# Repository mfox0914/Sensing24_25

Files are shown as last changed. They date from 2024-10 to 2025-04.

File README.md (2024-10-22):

# Olin Baja - 2022-2023 Electrical Projects

A variety of KiCAD schematics, PCBs, and other fun stuff from your favorite offroad vehicle team at Olin Collge of Engineering

## Current Projects
* SPI to CAN Board
	* Adapter board to convert from SPI sensor signals to CAN signals using a Raspberry Pi Pico
* Tachometer Board
	* Attempting to ressurect a techometer circut from a Baja project long ago.

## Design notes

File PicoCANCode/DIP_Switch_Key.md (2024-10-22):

## 2022 Olin Baja - DIP Switch Guide
DIP switches are assumed to be pulled LOW when active.

.

### **Ride Height - Front Driver Side**
DIP0        DIP1     DIP2        DIP3

0           0        0           0

CAN Address: 0x1111FFAA

### **Ride Height - Front Passenger Side**
DIP0        DIP1     DIP2        DIP3

1           0        0           0

CAN Address: 0x1111FFBB

### **Ride Height - Rear Driver Side**
DIP0        DIP1     DIP2        DIP3

0           1        0           0

CAN Address: 0x1111EEAA

### **Ride Height - Rear Passenger Side**
DIP0        DIP1     DIP2        DIP3

0           0        1           0

CAN Address: 0x1111EEBB

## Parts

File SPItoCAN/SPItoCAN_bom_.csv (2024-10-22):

Component | Description | Part | References | Value | Footprint | Quantity Per PCB | Datasheet | MFN | MPN | PurchasingLink | Digikey PN | Purchase Link
1 | Capacitor, 0.1uF, 50V, 5%, 0805 | C_0.1uF | C4 C5 | C_0.1uF | C_0805_OEM | 2 | http://datasheets.avx.com/X7RDielectric.pdf | DK | 478-3352-1-ND | https://www.digikey.com/products/en?keywords=478-3352-1-ND
2 | Capacitor, 10uF, 16V, 10%, 0805 | C_10uF_16V | C3 | C_10uF_16V | C_0805_OEM | 1 | http://www.samsungsem.com/kr/support/product-search/mlcc/__icsFiles/afieldfile/2016/01/15/Data%20sheet_CL21A106KOCLRNC.pdf | DK | 1276-2399-1-ND | https://www.digikey.com/product-detail/en/samsung-electro-mechanics/CL21A106KOCLRNC/1276-2399-1-ND/3890485
3 | Capacitor, 18pF, 10V, 1%, 0603 | C_18pF | C1 C2 | C_22pF | C_0603_1608Metric | 2 | https://www.vishay.com/docs/28548/vjw1bcbascomseries.pdf | DK | 720-1660-1-ND | https://www.digikey.com/product-detail/en/vishay-vitramon/VJ0603A180FXQCW1BC/720-1660-1-ND/8324080
4 | LED_0805_Red | LED_0805_Red | D1 | LED_0805_Red | LED_0805_Red | 1 | https://docs.broadcom.com/docs/AV02-0112EN | Avago | HSMC-C170 | https://www.digikey.com/product-detail/en/osram-opto-semiconductors-inc/LH-R974-LP-1/475-1415-1-ND/1802604 | 516-1428-1-ND
5 | CONN HEADER 2 POS 2.54mm | CONN_01x02 | J1 J2 J3 | CONN_01x02 | PinHeader_1x02_P2.54mm_Vertical | 3 | https://katalog.we-online.de/em/datasheet/6130xx11121.pdf | DK | 732-5315-ND
6 |  | Conn_01x07 | J4 | Conn_01x07 | PinHeader_1x07_P2.54mm_Vertical | 1 | https://www.we-online.com/katalog/datasheet/6130xx11121.pdf | Würth Elektronik | 61300711121 | https://www.digikey.com/en/products/detail/61300711121/732-5320-ND/4846837?curr=usd
7 |  | R_10K | R1 | R_10K | R_0805_OEM | 1 | http://www.bourns.com/data/global/pdfs/CRS.pdf | DK | CRS0805-FX-1002ELFCT-ND | https://www.digikey.com/products/en?keywords=CRS0805-FX-1002ELFCT-ND
8 |  | R_120 | R2 | R_120 | R_0805_OEM | 1 | https://www.mouser.com/datasheet/2/315/AOA0000C304-1149620.pdf | DK | 667-ERJ-6ENF1200V | https://www.mouser.com/ProductDetail/Panasonic-Industrial-Devices/ERJ-6ENF1200V
9 |  | R_1K | R3 | R_1K | R_0805_OEM | 1 | https://www.seielect.com/Catalog/SEI-rncp.pdf | DK | RNCP0805FTD1K00CT-ND | https://www.digikey.com/products/en?keywords=RNCP0805FTD1K00CT-ND
10 | Stand-Alone CAN Controller with SPI Interface, SOIC-18 | MCP2515-xSO | U2 | MCP2515-xSO | SOIC-18W_7.5x11.6mm_P1.27mm | 1 | https://ww1.microchip.com/downloads/en/DeviceDoc/MCP2515-Stand-Alone-CAN-Controller-with-SPI-20001801J.pdf |  | MCP2515T-I/SO | https://www.digikey.com/en/products/detail/microchip-technology/MCP2515T-I-SO/593681 | MCP2515T-I/SODKR-ND
11 |  | TJA1050T | U1 | TJA1051T-E | SOIC127P600X175-8N | 1 | https://www.mouser.com/datasheet/2/302/TJA1050-1127967.pdf |  | TJA1050T/CM,118 | https://www.mouser.com/ProductDetail/NXP-Semiconductors/TJA1050T-CM118?qs=5XOdhvmYM0NFFspw0VP5sA%3D%3D
12 | CRYSTAL 8.0000MHZ 18PF SMD | Crystal_8MHz | Y1 | Crystal_8MHz | ABM3-8_5.0x3.2mm_P3.7mm | 1 | https://abracon.com/Resonators/abm3.pdf | DK | 535-10630-1-ND | https://www.digikey.com/product-detail/en/abracon-llc/ABM3-8.000MHZ-D2Y-T/535-10630-1-ND/2344632
Component Groups: | 12
Component Count: | 16
Fitted Components: | 16
Number of PCBs: | 1
Total components: | 16
Schematic Version:
Schematic Date:
PCB Variant: | default
BoM Date: | 1/25/2023 20:43
Schematic Source: | SPItoCAN.kicad_sch
KiCad Version: | Eeschema (6.0.7)

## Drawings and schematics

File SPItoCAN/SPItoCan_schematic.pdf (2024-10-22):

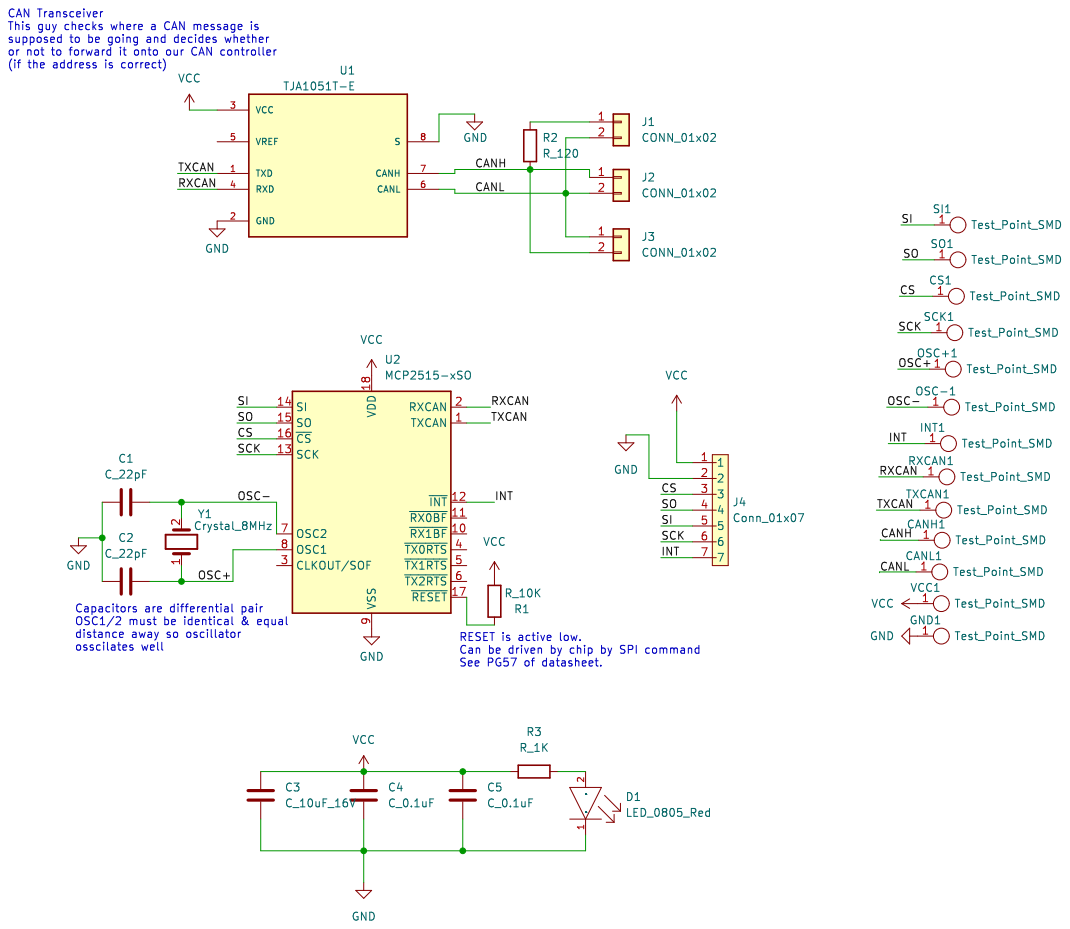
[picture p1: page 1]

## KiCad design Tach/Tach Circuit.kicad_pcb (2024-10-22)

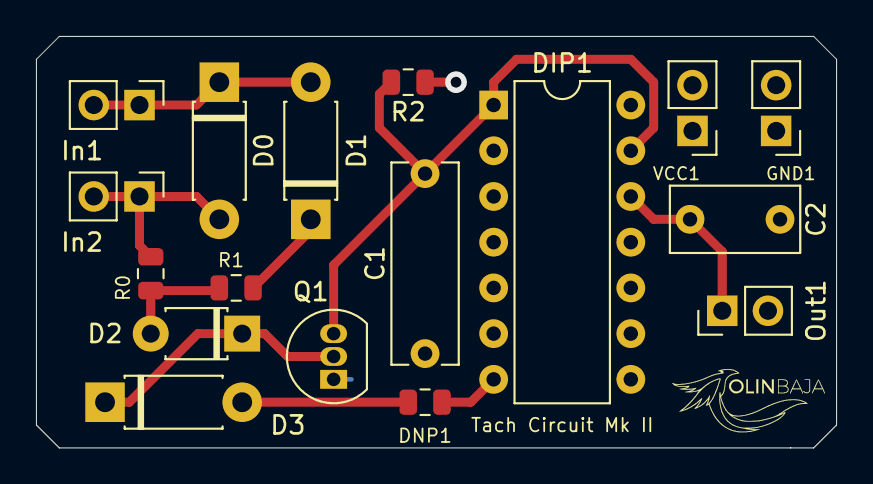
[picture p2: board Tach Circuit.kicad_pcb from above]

Board: 2 copper layers, 44.4 x 22.9 mm, 17 parts (0 on the bottom side), 10 nets.

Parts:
C1: 2200pF; C_Rect_L11.0mm_W3.5mm_P10.00mm_MKT
C2: 39nF; C_Rect_L7.0mm_W3.5mm_P5.00mm
D0, D1: 1N4007; D_DO-41_SOD81_P7.62mm_Horizontal
D2: 1N4148; D_T-1_P5.08mm_Horizontal
D3: 1N4738; D_DO-41_SOD81_P7.62mm_Horizontal
DIP1: SN74HC14N; DIP-14_W7.62mm
DNP1: DNP; R_0805_2012Metric
GND1: GND; PinHeader_1x02_P2.54mm_Vertical
In1: Vin +; PinHeader_1x02_P2.54mm_Vertical
In2: Vin-; PinHeader_1x02_P2.54mm_Vertical
Out1: Vout; PinHeader_1x02_P2.54mm_Vertical
Q1: 2N3904; TO-92_Inline
R0, R1: 10k; R_0805_2012Metric
R2: 4.7k; R_0805_2012Metric
VCC1: 5V; PinHeader_1x02_P2.54mm_Vertical

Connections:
+5V: DIP1.14, R2.1, VCC1.1
GND: C1.2, C2.2, DIP1.7, DNP1.2, GND1.1, Q1.1
unnamed: C1.1, DIP1.1, DIP1.13, Q1.3, R2.2
unnamed: C2.1, DIP1.12, Out1.1
unnamed: D0.1, D1.2, In1.1
unnamed: D0.2, In2.1, R0.1
unnamed: D1.1, R1.2
unnamed: D2.1, D3.1, Q1.2
unnamed: D2.2, R0.2, R1.1
unnamed: D3.2, DNP1.1

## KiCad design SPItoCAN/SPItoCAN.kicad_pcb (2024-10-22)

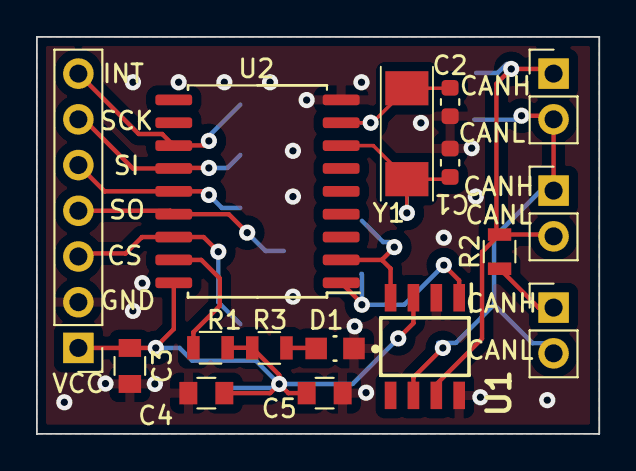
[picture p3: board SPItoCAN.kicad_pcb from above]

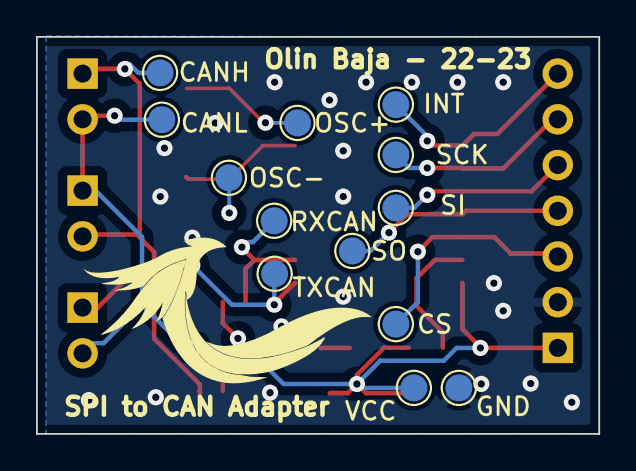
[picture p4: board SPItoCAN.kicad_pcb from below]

Board: 2 copper layers, 31.2 x 22.1 mm, 29 parts (13 on the bottom side), 16 nets.

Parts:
C1, C2: C_22pF; C_0603_1608Metric
C3: C_10uF_16V; C_0805_OEM
C4, C5: C_0.1uF; C_0805_OEM
CANH: Test_Point_SMD; TestPoint_Pad_D1.5mm
CANL: Test_Point_SMD; TestPoint_Pad_D1.5mm
CS: Test_Point_SMD; TestPoint_Pad_D1.5mm
D1: LED_0805_Red
GND: Test_Point_SMD; TestPoint_Pad_D1.5mm
INT: Test_Point_SMD; TestPoint_Pad_D1.5mm
J1, J2, J3: CONN_01x02; PinHeader_1x02_P2.54mm_Vertical
J4: Conn_01x07; PinHeader_1x07_P2.54mm_Vertical
OSC+: Test_Point_SMD; TestPoint_Pad_D1.5mm
OSC-: Test_Point_SMD; TestPoint_Pad_D1.5mm
R1: R_10K; R_0805_OEM
R2: R_120; R_0805_OEM
R3: R_1K; R_0805_OEM
RXCAN: Test_Point_SMD; TestPoint_Pad_D1.5mm
SCK: Test_Point_SMD; TestPoint_Pad_D1.5mm
SI: Test_Point_SMD; TestPoint_Pad_D1.5mm
SO: Test_Point_SMD; TestPoint_Pad_D1.5mm
TXCAN: Test_Point_SMD; TestPoint_Pad_D1.5mm
U1: TJA1051T-E; SOIC127P600X175-8N
U2: MCP2515-xSO; SOIC-18W_7.5x11.6mm_P1.27mm
VCC: Test_Point_SMD; TestPoint_Pad_D1.5mm
Y1: Crystal_8MHz; ABM3-8_5.0x3.2mm_P3.7mm

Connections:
/CANH: CANH.1, J2.1, J3.2, R2.2, U1.7 (CANH)
/CANL: CANL.1, J1.2, J2.2, J3.1, U1.6 (CANL)
/CS: CS.1, J4.3, U2.16 (~CS)
/INT: INT.1, J4.7, U2.12 (~INT)
/OSC+: C2.2, OSC+.1, U2.8 (OSC1), Y1.1
/OSC-: C1.2, OSC-.1, U2.7 (OSC2), Y1.2
/RXCAN: RXCAN.1, U1.4 (RXD), U2.2 (RXCAN)
/SCK: J4.6, SCK.1, U2.13 (SCK)
/SI: J4.5, SI.1, U2.14 (SI)
/SO: J4.4, SO.1, U2.15 (SO)
/TXCAN: TXCAN.1, U1.1 (TXD), U2.1 (TXCAN)
GND: C1.1, C2.1, C3.2, C4.2, C5.2, D1.1 (CATHODE), GND.1, J4.2, U1.2 (GND), U1.8 (S), U2.9 (VSS)
unnamed: D1.2 (ANODE), R3.2
unnamed: J1.1, R2.1
unnamed: R1.1, U2.17 (~RESET)
VCC: C3.1, C4.1, C5.1, J4.1, R1.2, R3.1, U1.3 (VCC), U2.18 (VDD), VCC.1

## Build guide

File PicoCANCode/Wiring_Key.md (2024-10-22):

# Olin Baja 2022 - Pico Wiring Key

## **DIP Switches**

GP11 - DIP0

GP10 - DIP1

GP9 - DIP2

GP8 - DIP3

(with all other sides of the DIP switch being connected to GND)

## **SPI to CAN Module**

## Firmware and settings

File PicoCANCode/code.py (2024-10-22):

from time import sleep
import board
import busio
from digitalio import DigitalInOut, Direction, Pull
from adafruit_mcp2515.canio import Message, RemoteTransmissionRequest
from adafruit_mcp2515 import MCP2515 as CAN
from analogio import AnalogIn

# Dictionary to convert between DIP switch positions and CAN IDs. Keys are
# tuples representing the values of 4 DIP switches.
#
# Pins default being pulled high, so a pin is pulled to GND and represented by
# "false" when the DIP switch is toggled on
DIP_TO_CAN_ID = {
    (True, True, True, True)  : 0x1111FFAA,
    (False, True, True, True) : 0x1111FFBB,
    (True, False, True, True) : 0x1111EEAA,
    (True, True, False, True) : 0x1111EEBB
}

# Configure DIP Switch inputs
dip0 = DigitalInOut(board.GP11)
dip1 = DigitalInOut(board.GP10)
dip2 = DigitalInOut(board.GP9)
dip3 = DigitalInOut(board.GP8)

# Add all DIP switches to a list to make it easier to assign properties to each
dip_switches = [dip0, dip1, dip2, dip3]

# Define ride height sensor analog input pin
sensor_in = AnalogIn(board.A0)

for switch in dip_switches:
    # Set each DIP switch as an input
    switch.direction = Direction.INPUT
    # Use an integrated pull-up resistor to prevent pins from floating; requires
    # pins to be pulled to GND in order to be active
    switch.pull = Pull.UP

# Determine CAN address (board identity) based on DIP switch position
dip_positions = (dip0.value, dip1.value, dip2.value, dip3.value)
try:
    can_id = DIP_TO_CAN_ID[dip_positions]
    print(f"Successfully set CAN ID. Current ID is: f{can_id}")
except KeyError:
    print("Invalid DIP position. Defaulting to CAD address of 0x00000000")
    can_id = "0x00000000"



cs = DigitalInOut(board.GP21)
cs.switch_to_output()
spi = busio.SPI(board.GP18, board.GP19, board.GP20)

# adafruit note: use loopback to test without another device
can_bus = CAN(spi, cs, loopback=True, silent=True)  

while True:
    with can_bus.listen(timeout=1.0) as listener:

        print(f"Current Sensor Value: {sensor_in.value}")
        message = Message(id=can_id, data=b"adafruit", extended=True)
        send_success = can_bus.send(message)
        print("Send success:", send_success)
        message_count = listener.in_waiting()
        print(message_count, "messages available")
        for _i in range(message_count):
            msg = listener.receive()
            print("Message from ", hex(msg.id))
            if isinstance(msg, Message):
                print("message data:", msg.data)
            if isinstance(msg, RemoteTransmissionRequest):
                print("RTR length:", msg.length)
    sleep(1)

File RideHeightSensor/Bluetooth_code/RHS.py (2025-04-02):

import aioble
import bluetooth
import asyncio
import struct
from sys import exit
from machine import ADC, Pin

# Define UUIDs for the service and characteristic
_SERVICE_UUID = bluetooth.UUID(0x1848)
_CHARACTERISTIC_UUID = bluetooth.UUID(0x2A6E)

# Initialize ADC for the potentiometer
pot = ADC(Pin(26))  # GPIO 26 (ADC0)

# IAM = "Central" # Change to 'Peripheral' or 'Central'
IAM = "RHS"

if IAM not in ['RHS','Central']:
    print("IAM must be either RHS or Central")
    exit()

if IAM != "Central":
    IAM_SENDING_TO = "Central"
     

# Bluetooth parameters
BLE_NAME = f"{IAM}"  # You can dynamically change this if you want unique names
BLE_SVC_UUID = bluetooth.UUID(0x181A)
BLE_CHARACTERISTIC_UUID = bluetooth.UUID(0x2A6E)
BLE_APPEARANCE = 0x0300
BLE_ADVERTISING_INTERVAL = 2000
BLE_SCAN_LENGTH = 5000
BLE_INTERVAL = 30000
BLE_WINDOW = 30000

# State Variables
message_count = 0

def encode_message(message):
    """ Encode a message to bytes """
    return message.encode('utf-8')

def decode_message(message):
    """ Decode a message from bytes """
    return message.decode('utf-8')

async def send_data_task(connection, characteristic):
    """ Send data to the connected device """
    global message_count
    while True:
        if not connection:
            print("error - no connection in send data")
            continue

        if not characteristic:
            print("error no characteristic provided in send data")
            continue
        # Message should be code to read RHS value
        message = f"{pot.read_u16()} Time: {message_count}"
        message_count +=1
        print(f"sending {message}")



async def receive_data_task(characteristic):
    """ Receive data from the connected device """
    global message_count
    while True:
        try:
            data = await characteristic.read()

            if data:
                print(f"{IAM} received: {decode_message(data)}, count: {message_count}")
                await characteristic.write(encode_message("Got it"))

            message_count += 1

        except asyncio.TimeoutError:
            print("Timeout waiting for data in {ble_name}.")
            break
        except Exception as e:
            print(f"Error receiving data: {e}")
            break

async def run_peripheral_mode():
    """ Run the peripheral mode """

    # Set up the Bluetooth service and characteristic
    ble_service = aioble.Service(BLE_SVC_UUID)
    characteristic = aioble.Characteristic(
        ble_service,
        BLE_CHARACTERISTIC_UUID,
        read=True,
        notify=True,
        write=True,
        capture=True,
    )
    aioble.register_services(ble_service)

    print(f"{BLE_NAME} starting to advertise")

    while True:
        async with await aioble.advertise(
            BLE_ADVERTISING_INTERVAL,
            name=BLE_NAME,
            services=[BLE_SVC_UUID],
            appearance=BLE_APPEARANCE) as connection:
            print(f"{BLE_NAME} connected to another device: {connection.device}")

            tasks = [
                asyncio.create_task(send_data_task(connection, characteristic)),
            ]
            await asyncio.gather(*tasks)
            print(f"{IAM} disconnected")
            break

async def ble_scan():
    """ Scan for a BLE device with the matching service UUID """

    print(f"Scanning for BLE Beacon named {BLE_NAME}...")

    async with aioble.scan(5000, interval_us=30000, window_us=30000, active=True) as scanner:
        async for result in scanner:
            if result.name() == IAM_SENDING_TO and BLE_SVC_UUID in result.services():
                print(f"found {result.name()} with service uuid {BLE_SVC_UUID}")
                return result
    return None

async def run_central_mode():
    """ Run the central mode """

    # Start scanning for a device with the matching service UUID
    while True:
        device = await ble_scan()

        if device is None:
            continue
        print(f"device is: {device}, name is {device.name()}")

        try:
            print(f"Connecting to {device.name()}")
            connection = await device.device.connect()

        except asyncio.TimeoutError:
            print("Timeout during connection")
            continue

        print(f"{IAM} connected to {connection}")

        # Discover services
        async with connection:
            try:
                service = await connection.service(BLE_SVC_UUID)
                characteristic = await service.characteristic(BLE_CHARACTERISTIC_UUID)
            except (asyncio.TimeoutError, AttributeError):
                print("Timed out discovering services/characteristics")
                continue
            except Exception as e:
                print(f"Error discovering services {e}")
                await connection.disconnect()
                continue

            tasks = [
                asyncio.create_task(receive_data_task(characteristic)),
            ]
            await asyncio.gather(*tasks)

            await connection.disconnected()
            print(f"{BLE_NAME} disconnected from {device.name()}")
            break

async def main():
    """ Main function """
    while True:
        if IAM == "Central":
            tasks = [
                asyncio.create_task(run_central_mode()),
            ]
        else:
            tasks = [
                asyncio.create_task(run_peripheral_mode()),
            ]

        await asyncio.gather(*tasks)

asyncio.run(main())

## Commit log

2022-09-28 Created SPI to CAN schematic and board design
2022-10-05 Added SPI to CAN schematic and PCB KiCAD files
    [SPItoCAN.kicad_pcb, SPItoCAN.kicad_sch]
2022-10-18 Cleaned up PCB layout, added ground plane
    [SPItoCAN.kicad_pcb, SPItoCAN.kicad_sch]
2022-10-19 cleaned up pcb, improved silkscreen, ran test gerber export
    [SPItoCAN.kicad_pcb, SPItoCAN.kicad_sch]
2022-10-27 cleaned up layout; replaced LED; generated BOM
    [SPItoCAN-B_Cu.gbr, SPItoCAN-B_Mask.gbr, SPItoCAN-B_Paste.gbr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]
2022-11-03 Imported tach circut
    [Tach Circuit.kicad_pcb, Tach Circuit.kicad_sch, Tach Circuit.sch]
2022-11-10 Fixed some wiring & routing across the board; added explanatory notes to schematic
    [SPItoCAN.kicad_pcb, SPItoCAN.kicad_sch]
2022-12-06 Added test for Pico W's
2022-12-13 Began tweaks to make everything fit within JLCPCB capabilites
    [SPItoCAN.kicad_pcb]
2023-01-25 Further updated PCB to meet JLCPCB capabilites. Pushing etc. Tach files
    [SPItoCAN.kicad_pcb]
2023-02-08 Final updates and gerber for board production
    Updated so board fits into breadboard and other misc. updates before generating gerbers
    [SPItoCAN-B_Cu.gbr, SPItoCAN-B_Mask.gbr, SPItoCAN-B_Paste.gbr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]
2023-02-08 Inital schematic for ride height sensor protoboard
    [RideHeightSensor.kicad_pcb, RideHeightSensor.kicad_sch]
2023-03-09 Add PicoCANCode base
    [RideHeightSensor.kicad_sch]
2023-03-21 Update .gitignore, Add SPItoCAN Schematic
2023-03-21 Add ability to set board identity by DIP switch
2023-04-20 Update firmware to work with DIP switches
2023-04-25 Update RHS schematic
    [RideHeightSensor.kicad_sch]
2025-03-12 Adding Ride Height Sensor BLE code - currently not working
    [RHS.py]
